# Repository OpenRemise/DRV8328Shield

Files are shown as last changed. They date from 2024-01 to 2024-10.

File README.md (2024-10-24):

# DRV8328Shield

RevA errors:
- PVDD should be tied to VIN instead of 5V  
  5V is simply too low to keep the high side switched on continuously

- TPS27S100B doesn't turn off if two consecutive shorts are too close together  
  This is also an issue for the ACK detection. The second ACK would simply get lost in this case:  
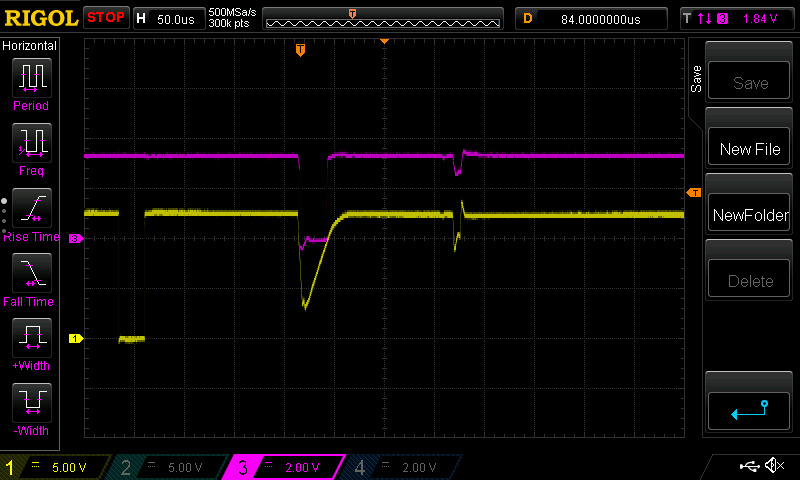
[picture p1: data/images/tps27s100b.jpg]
tps27s100b
    

  The only reliable fix for this might be to monitor IMON as well. Here is a capture of the second ACK pulse of an MX645 during a DECUP update. IMON is above 500mV for about 8µs.
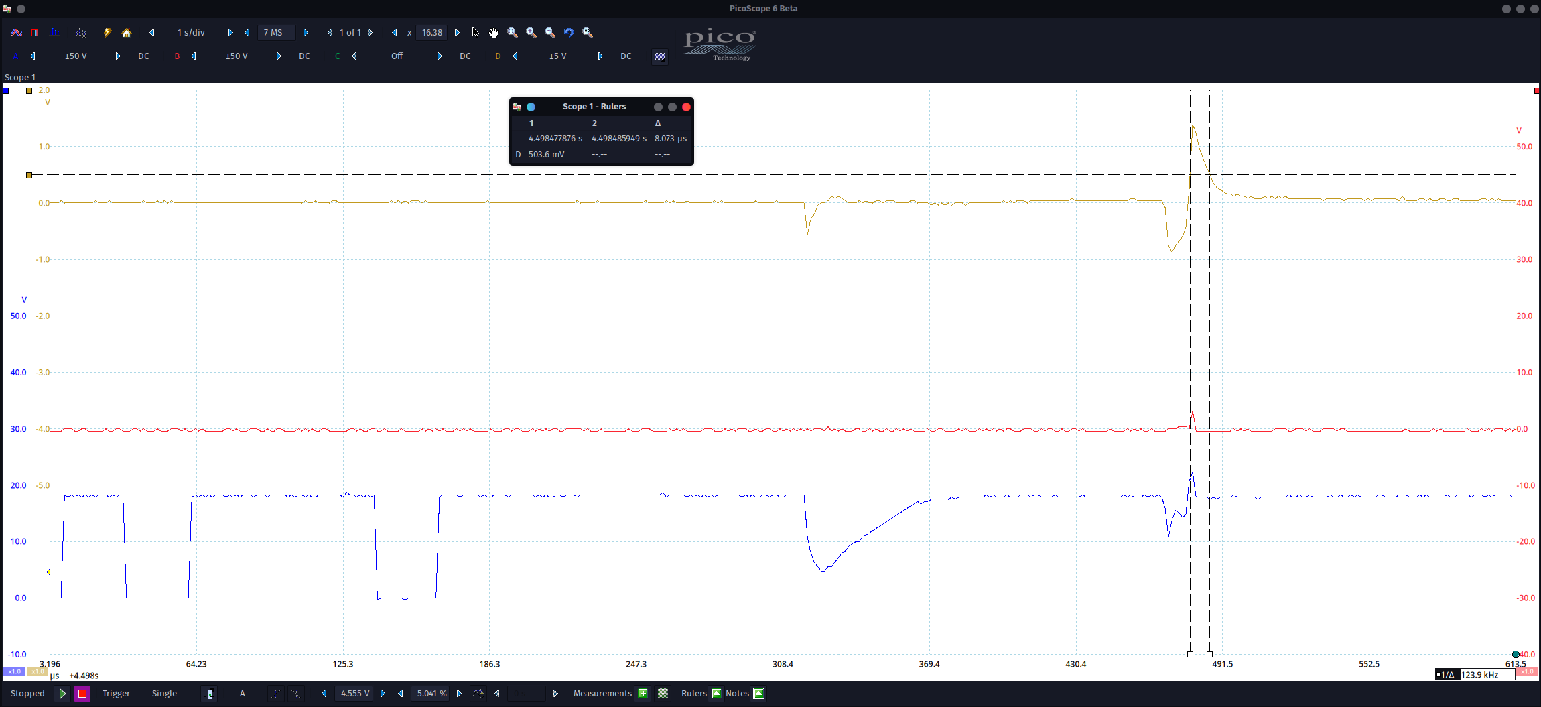
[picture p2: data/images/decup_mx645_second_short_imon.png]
decup_mx645_second_short_imon
    

  As it turns it this isn't a workaround either. While some shorts look like this  
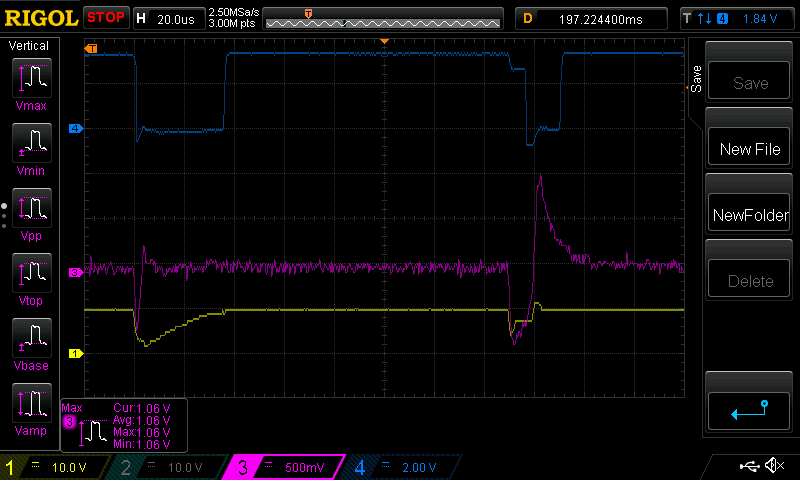
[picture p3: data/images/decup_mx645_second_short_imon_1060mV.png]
decup_mx645_second_short_imon_1060mV
    

  Others look like this  
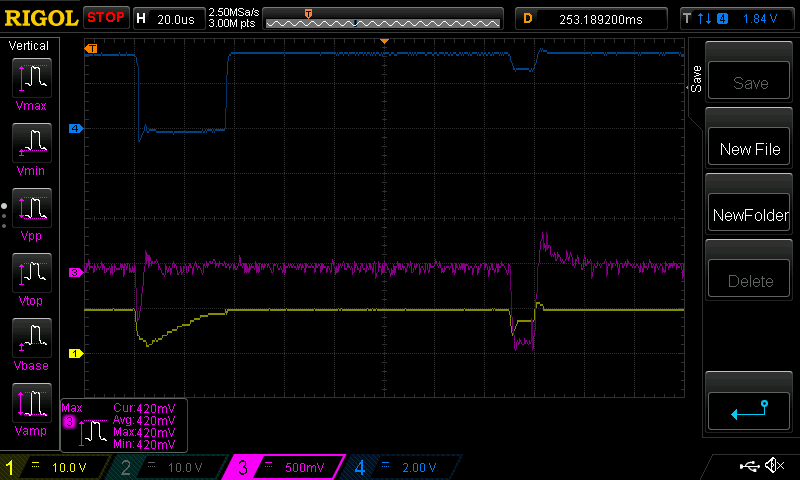
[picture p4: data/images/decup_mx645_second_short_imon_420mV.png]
decup_mx645_second_short_imon_420mV
    
  And that 420mV pulse is too short for a common LM339... now what?

- TPS27S100B could use another 1µF ceramic capacitor at IN (e.g. same as at OUT)

- N and P tracks are reversed  
  We currently generate the signal for INHA (output SHA) with the first half-bit 1 and the second half-bit 0. It must stay that way because we want the RMT end-of-transmission level to be 0. The problem is that a signal with the first half-bit 1 would mark the P and not the N track. Currently we feed SHA into the N pin though.  
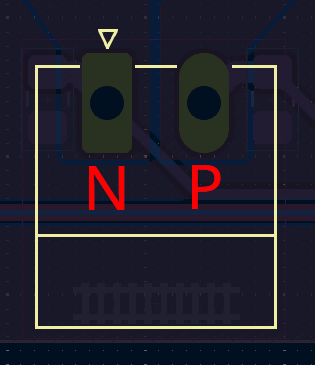
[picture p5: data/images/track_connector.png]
track


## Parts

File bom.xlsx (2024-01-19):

 |  |  | DRV8328Shield PCS BOM
Item # | *Designator | *Qty | Manufacturer | *Mfg Part # | Description / Value | *Package/Footprint | Type | Your Instructions / Notes
1 | C1, C5, C6, C14, C22 | 5 | Samsung Electro-Mechanics | CL05B104KB54PNC | CAP CER 0.1UF 50V X7R 0402 | 0402 | SMD
2 | C2, C4, C9, C10, C13, C18, C19, C21 | 8 | Murata Electronics | GRM1555C2A102JE01D | CAP CER 1000PF 100V C0G/NP0 0402 | 0402 | SMD
3 | C3 | 1 | Murata Electronics | GCM1555C1H221JA16D | CAP CER 220PF 50V C0G/NP0 0402 | 0402 | SMD
4 | C7, C8 | 2 | Murata Electronics | GCM1555C1H101JA16D | CAP CER 100PF 50V C0G/NP0 0402 | 0402 | SMD
5 | C11 | 1 | Murata Electronics | GRM31MR72A474KA35L | CAP CER 0.47UF 100V X7R 1206 | 1206 | SMD
6 | C12 | 1 | Samsung Electro-Mechanics | CL31B106KBHNNNE | CAP CER 10UF 50V X7R 1206 | 1206 | SMD
7 | C15, C23 | 2 | Nichicon | UCL1V101MCL6GS | CAP ALUM 100UF 20% 35V SMD | 6.60x6.60mm | SMD
8 | C16, C17, C20, C24 | 4 | Samsung Electro-Mechanics | CL31B105KCHVPJE | CAP CER 1UF 100V X7R 1206 | 1206 | SMD
9 | D1, D2, D4, D6, D7, D8, D9, D10, D11, D12 | 10 | onsemi | 1N4148WT | SMALL SIGNAL DIODE SOD523 100V | SOD-523 | SMD
10 | D3 | 1 | Diotec Semiconductor | BZX84C15 | DIODE ZENER 15V 300W SOT23-3 | SOT-23-3 | SMD
11 | D5 | 1 | Toshiba Semiconductor and Storage | CEZ30V,L3F | TVS DIODE 30VWM 47.5VC ESC | SOD-523
12 | J1 | 1 | Phoenix Contact | 1836189 | TERM BLOCK HDR 2POS 90DEG 5.08MM | not fitted | not fitted
13 | J2 | 1 | Phoenix Contact | 1844210 | TERM BLOCK HDR 2POS 90DEG 3.5MM | not fitted | not fitted
14 | J3 | 1 |  |  |  | not fitted | not fitted
15 | JP1 | 1 |  |  |  | not fitted | not fitted
16 | JP2 | 1 |  |  |  | not fitted | not fitted
17 | Q1, Q3, Q4, Q6, Q7 | 5 | Vishay Siliconix | SIS4634LDN-T1-GE3 | N-CHANNEL 60 V (D-S) MOSFET POWE | PowerPAK® 1212-8 | SMD
18 | Q2, Q8 | 2 | Rohm Semiconductor | QS6K21TR | MOSFET 2N-CH 45V 1A TSMT6 | TSOT-23-6 | SMD
19 | Q5, Q10 | 2 | ANBON SEMICONDUCTOR (INT'L) LIMITED | BC847B | PLASTIC ENCAPSULATE TRANSISTORS | SOT-23-3 | SMD
20 | Q9 | 1 | Diotec Semiconductor | BC857B | BJT SOT-23 45V 100MA | SOT-23-3 | SMD
21 | R1, R2, R3, R4, R43 | 5 | YAGEO | RC0402FR-0722KL | RES 22K OHM 1% 1/16W 0402 | 0402 | SMD
22 | R5, R11, R24, R26, R28, R34, R35, R45 | 8 | YAGEO | RC0402FR-0710KL | RES 10K OHM 1% 1/16W 0402 | 0402 | SMD
23 | R6, R7, R8 | 3 | YAGEO | RC0402FR-07100RL | RES 100 OHM 1% 1/16W 0402 | 0402 | SMD
24 | R9, R10, R36, R42, R44 | 5 | YAGEO | RC0402FR-074K7L | RES 4.7K OHM 1% 1/16W 0402 | 0402 | SMD
25 | R12 | 1 | Vishay Dale | RCS08052R20FKEA | RES SMD 2.2 OHM 1% 1/2W 0805 | 0805 | SMD
26 | R13, R14, R19, R27, R31, R37, R41 | 7 | YAGEO | RC0402FR-071KL | RES 1K OHM 1% 1/16W 0402 | 0402 | SMD
27 | R15, R18 | 2 | Stackpole Electronics Inc | RMCF0805FT4K70 | RES 4.7K OHM 1% 1/8W 0805 | not fitted | not fitted
28 | R16, R17 | 2 | YAGEO | RC0402FR-073K3L | RES 3.3K OHM 1% 1/16W 0402 | 0402 | SMD
29 | R20, R21 | 2 | YAGEO | RC0402FR-0733RL | RES 33 OHM 1% 1/16W 0402 | 0402 | SMD
30 | R22 | 1 | YAGEO | RC0402FR-13220RL | RES 220 OHM 1% 1/16W 0402 | 0402 | SMD
31 | R23, R25, R32, R33 | 4 | YAGEO | RC0402FR-0747RL | RES 47 OHM 1% 1/16W 0402 | 0402 | SMD
32 | R29 | 1 | YAGEO | RC0402FR-07100KL | RES 100K OHM 1% 1/16W 0402 | 0402 | SMD
33 | R30 | 1 | Stackpole Electronics Inc | RMCF0805FT220R | RES 220 OHM 1% 1/8W 0805 | 0805 | SMD
34 | R38 | 1 | YAGEO | RC0402FR-07120RL | RES 120 OHM 1% 1/16W 0402 | 0402 | SMD
35 | R39 | 1 | YAGEO | RC0402FR-072K2L | RES 2.2K OHM 1% 1/16W 0402 | 0402 | SMD
36 | R40 | 1 | YAGEO | RC0402FR-075K1L | RES 5.1K OHM 1% 1/16W 0402 | 0402 | SMD
37 | TP1, TP2, TP3, TP4, TP5, TP6, TP7, TP8, TP9, TP10, TP11, TP12 |  |  |  |  | not fitted | not fitted
38 | U1 | 1 | onsemi | LM393EDR2G | IC COMPARATOR 2 GEN PUR 8SOIC | 8-SOIC | SMD
39 | U2 | 1 | Nexperia USA Inc. | 74LVC02APW,118 | IC GATE NOR 4CH 2-INP 14TSSOP | 14-TSSOP | SMD
40 | U3 | 1 | Texas Instruments | TLV9051IDBVR | IC OPAMP GP 1 CIRCUIT SOT23-5 | SOT23-5 | SMD
41 | U4 | 1 | Texas Instruments | DRV8328BRUYR | 60 V 1000/2000 MA 3-PHASE GATE D | 28-WQFN | SMD
42 | U5 | 1 | Texas Instruments | TPS27S100BPWPR | IC PWR DRVR N-CHAN 1:1 14HTSSOP | 14-HTSSOP | SMD

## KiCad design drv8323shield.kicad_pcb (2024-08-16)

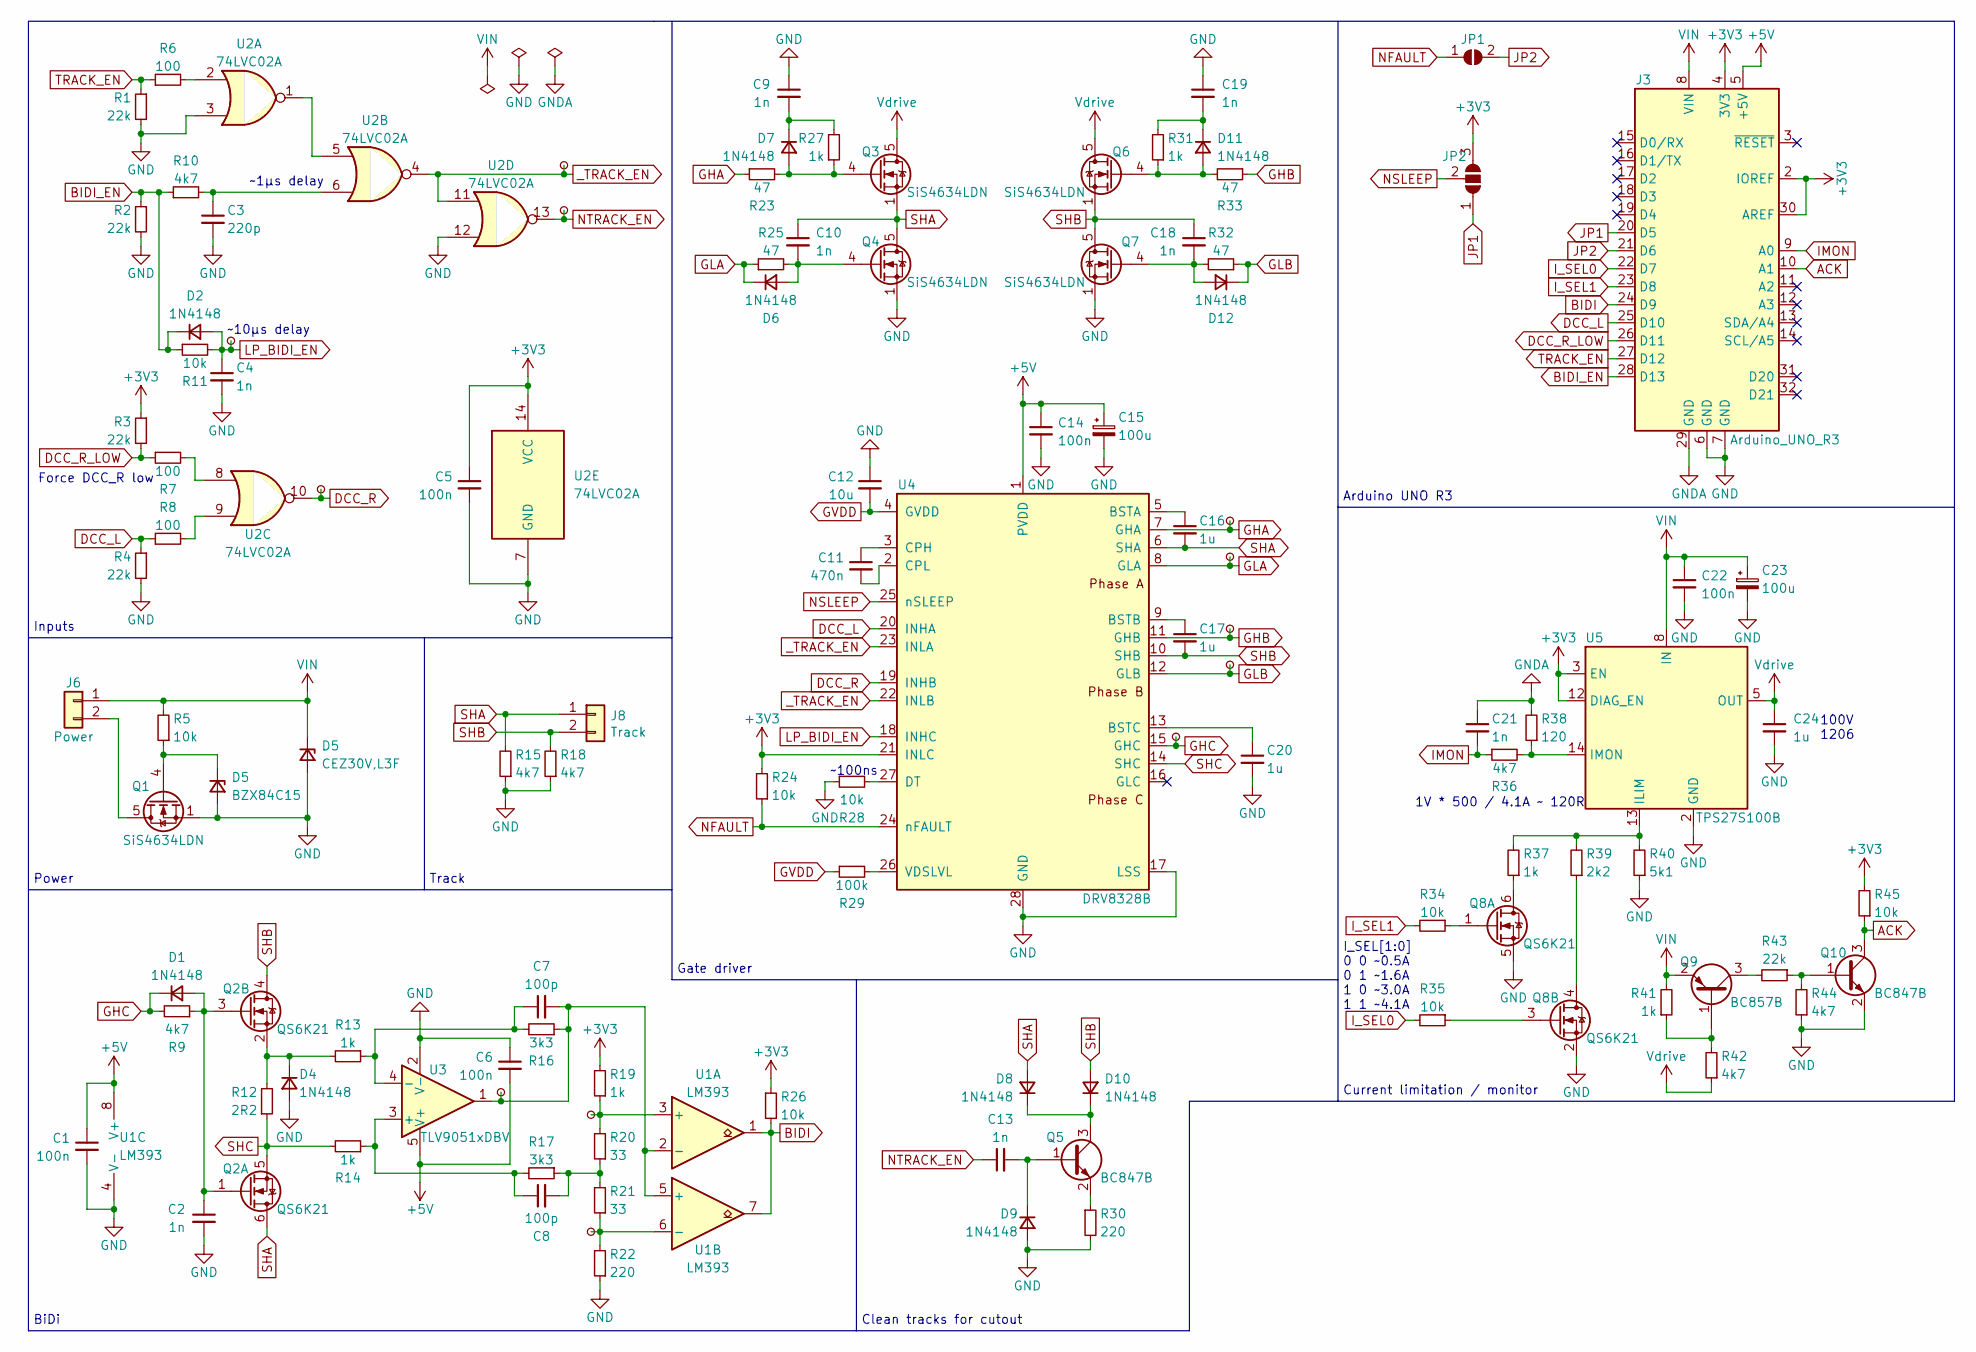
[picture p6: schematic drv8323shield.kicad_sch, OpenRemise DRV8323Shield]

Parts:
C1, C5, C6, C14, C22: 100n; C_0402_1005Metric
C2, C4, C9, C10, C13, C18, C19, C21: 1n; C_0402_1005Metric
C3: 220p; C_0402_1005Metric
C7, C8: 100p; C_0402_1005Metric
C11: 470n; C_1206_3216Metric
C12: 10u; C_1206_3216Metric
C15, C23: 100u; CP_Elec_6.3x7.7
C16, C17, C20, C24: 1u; C_1206_3216Metric
D1, D2, D4, D6, D7, D8, D9, D10, D11, D12: 1N4148; D_SOD-523
D5: CEZ30V,L3F; D_SOD-523
J3: Arduino_UNO_R3; Arduino_UNO_R3_WithMountingHoles
J6: Power; PhoenixContact_MC_1,5_2-G-5.08_1x02_P5.08mm_Horizontal
J8: Track; PhoenixContact_MC_1,5_2-G-3.5_1x02_P3.50mm_Horizontal
JP1: SolderJumper_2_Open; SolderJumper-2_P1.3mm_Open_Pad1.0x1.5mm
JP2: SolderJumper_3_Open; SolderJumper-3_P1.3mm_Open_Pad1.0x1.5mm
Q1, Q3, Q4, Q6, Q7: SiS4634LDN; Vishay_PowerPAK_1212-8_Single
Q2, Q8: QS6K21; TSOT-23-6
Q5, Q10: BC847B; SOT-23
Q9: BC857B; SOT-23-3
R1, R2, R3, R4, R43: 22k; R_0402_1005Metric
R5, R11, R24, R26, R28, R34, R35, R45: 10k; R_0402_1005Metric
R6, R7, R8: 100; R_0402_1005Metric
R9, R10, R36, R42, R44: 4k7; R_0402_1005Metric
R12: 2R2; R_0805_2012Metric_Pad1.20x1.40mm_HandSolder
R13, R14, R19, R27, R31, R37, R41: 1k; R_0402_1005Metric
R15, R18: 4k7; R_0805_2012Metric_Pad1.20x1.40mm_HandSolder
R16, R17: 3k3; R_0402_1005Metric
R20, R21: 33; R_0402_1005Metric
R22: 220; R_0402_1005Metric
R23, R25, R32, R33: 47; R_0402_1005Metric
R29: 100k; R_0402_1005Metric
R30: 220; R_0805_2012Metric_Pad1.20x1.40mm_HandSolder
R38: 120; R_0402_1005Metric
R39: 2k2; R_0402_1005Metric
R40: 5k1; R_0402_1005Metric
TP1, TP2, TP3, TP4, TP5, TP6, TP7, TP8, TP9, TP10, TP11, TP12: TestPoint_Small; TestPoint_Pad_1.0x1.0mm
U1: LM393; SOIC-8_3.9x4.9mm_P1.27mm
U2: 74LVC02A; TSSOP-14_4.4x5mm_P0.65mm
U3: TLV9051xDBV; SOT-23-5
U4: DRV8328B; QFN-28-1EP_4x4mm_P0.4mm_EP2.6x2.6mm_ThermalVias
U5: TPS27S100B; HTSSOP-14-1EP_4.4x5mm_P0.65mm_EP3.4x5mm_Mask3x3.1mm_Thermal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

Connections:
+3V3: C5.1, J3.2 (IOREF), J3.4 (3V3), J3.30 (AREF), JP2.3 (B), R3.1, R19.2, R24.2, R26.1, R45.2, U2.14 (VCC), U4.21 (INLC), U5.3 (EN), U5.12 (DIAG_EN)
+5V: C1.1, C6.2, C14.1, C15.1, J3.5 (+5V), U1.8 (V+), U3.5 (V+), U4.1 (PVDD)
ACK: J3.10 (A1), Q10.3 (C), R45.1
BIDI: J3.24 (D9), R26.2, U1.1, U1.7
BIDI_EN: D2.1 (K), J3.28 (D13), R2.1, R10.1, R11.1
DCC_L: J3.25 (D10), R4.1, R8.1, U4.20 (INHA)
DCC_R: TP2.1, U2.10, U4.19 (INHB)
DCC_R_LOW: J3.26 (D11), R3.2, R7.1
GHA: R23.1, TP9.1, U4.7 (GHA)
GHB: R33.1, TP11.1, U4.11 (GHB)
GHC: D1.1 (K), R9.2, TP8.1, U4.15 (GHC)
GLA: D6.1 (K), R25.1, TP10.1, U4.8 (GLA)
GLB: D12.1 (K), R32.1, TP12.1, U4.12 (GLB)
GND: C1.2, C2.2, C3.2, C4.2, C5.2, C6.1, C9.1, C12.1, C14.2, C15.2, C19.1, C20.2, C22.2, C23.2, C24.2, D4.2 (A), D5.2 (A), D9.2 (A), J3.6 (GND), J3.7 (GND), Q1.1 (S), Q1.2 (S), Q1.3 (S), Q4.1 (S), Q4.2 (S), Q4.3 (S), Q7.1 (S), Q7.2 (S), Q7.3 (S), Q8.2 (S), Q8.5 (S), Q10.2 (E), R1.2, R2.2, R4.2, R15.1, R18.1, R22.1, R28.1, R30.2, R40.1, R44.1, U1.4 (V-), U2.3, U2.7 (GND), U2.12, U3.2 (V-), U4.17 (LSS), U4.28 (GND), U4.29 (GND), U5.2 (GND), U5.15 (GND); also elsewhere on the board
GNDA: C21.1, J3.29 (GND), R38.2
GVDD: C12.2, R29.1, U4.4 (GVDD)
IMON: C21.2, J3.9 (A0), R36.1
I_SEL0: J3.22 (D7), R35.2
I_SEL1: J3.23 (D8), R34.2
JP1: J3.20 (D5), JP2.1 (A)
JP2: J3.21 (D6), JP1.2 (B)
LP_BIDI_EN: C4.1, D2.2 (A), R11.2, TP1.1, U4.18 (INHC)
NFAULT: JP1.1 (A), R24.1, U4.24 (nFAULT)
NSLEEP: JP2.2 (C), U4.25 (nSLEEP)
NTRACK_EN: C13.1, TP5.1, U2.13
unnamed: C3.1, R10.2, U2.6
unnamed: C8.2, R17.1, R20.1, R21.2
unnamed: C2.1, D1.2 (A), Q2.1 (G), Q2.3 (G), R9.1
unnamed: D4.1 (K), Q2.2 (S), R12.2, R13.2
unnamed: C10.2, D6.2 (A), Q4.4 (G), R25.2
unnamed: D7.2 (A), Q3.4 (G), R23.2, R27.1
unnamed: C9.2, D7.1 (K), R27.2
unnamed: C13.2, D9.1 (K), Q5.1 (B)
unnamed: D8.1 (K), D10.1 (K), Q5.3 (C)
unnamed: D11.2 (A), Q6.4 (G), R31.1, R33.2
unnamed: C19.2, D11.1 (K), R31.2
unnamed: C18.2, D12.2 (A), Q7.4 (G), R32.2
unnamed 37: Q1.5 (D); also elsewhere on the board
unnamed: Q5.2 (E), R30.1
unnamed: Q8.6 (D), R37.1
unnamed: Q8.1 (G), R34.1
unnamed: Q8.4 (D), R39.1
unnamed: Q8.3 (G), R35.1
unnamed: Q9.1 (B), R41.1, R42.2
unnamed: Q9.3 (C), R43.2
unnamed: Q10.1 (B), R43.1, R44.2
unnamed: R6.2, U2.2
unnamed: R7.2, U2.8
unnamed: R8.2, U2.9
unnamed: R19.1, R20.2, TP6.1, U1.3 (+)
unnamed: C7.2, R16.1, TP3.1, U1.2 (-), U1.5 (+), U3.1
unnamed: R21.1, R22.2, TP7.1, U1.6 (-)
unnamed: U2.1, U2.5
unnamed: C8.1, R14.1, R17.2, U3.3 (+)
unnamed: C7.1, R13.1, R16.2, U3.4 (-)
unnamed: C16.1, U4.5 (BSTA)
unnamed: C17.1, U4.9 (BSTB)
unnamed: C20.1, U4.13 (BSTC)
unnamed: C11.1, U4.3 (CPH)
unnamed: C11.2, U4.2 (CPL)
unnamed: R28.2, U4.27 (DT)
unnamed: R29.2, U4.26 (VDSLVL)
unnamed: R37.2, R39.2, R40.2, U5.13 (ILIM)
unnamed: R36.2, R38.1, U5.14 (IMON)
SHA: C10.1, C16.2, D8.2 (A), Q2.6 (D), Q3.1 (S), Q3.2 (S), Q3.3 (S), Q4.5 (D), R15.2, U4.6 (SHA); also elsewhere on the board
SHB: C17.2, C18.1, D10.2 (A), Q2.4 (D), Q6.1 (S), Q6.2 (S), Q6.3 (S), Q7.5 (D), R18.2, U4.10 (SHB); also elsewhere on the board
SHC: Q2.5 (S), R12.1, R14.2, U4.14 (SHC)
TRACK_EN: J3.27 (D12), R1.1, R6.1
Vdrive: C24.1, Q3.5 (D), Q6.5 (D), R42.1, U5.5 (OUT), U5.6 (OUT), U5.7 (OUT)
_TRACK_EN: TP4.1, U2.4, U2.11, U4.22 (INLB), U4.23 (INLA)

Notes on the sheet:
Track
Inputs
Clean tracks for cutout
~10µs delay
BiDi
1V * 500 / 4.1A ~ 120R
Gate driver
Current limitation / monitor
100V 1206
Power
Force DCC_R low
~100ns
I_SEL[1:0] 0 0 ~0.5A 0 1 ~1.6A 1 0 ~3.0A 1 1 ~4.1A
Arduino UNO R3
~1µs delay

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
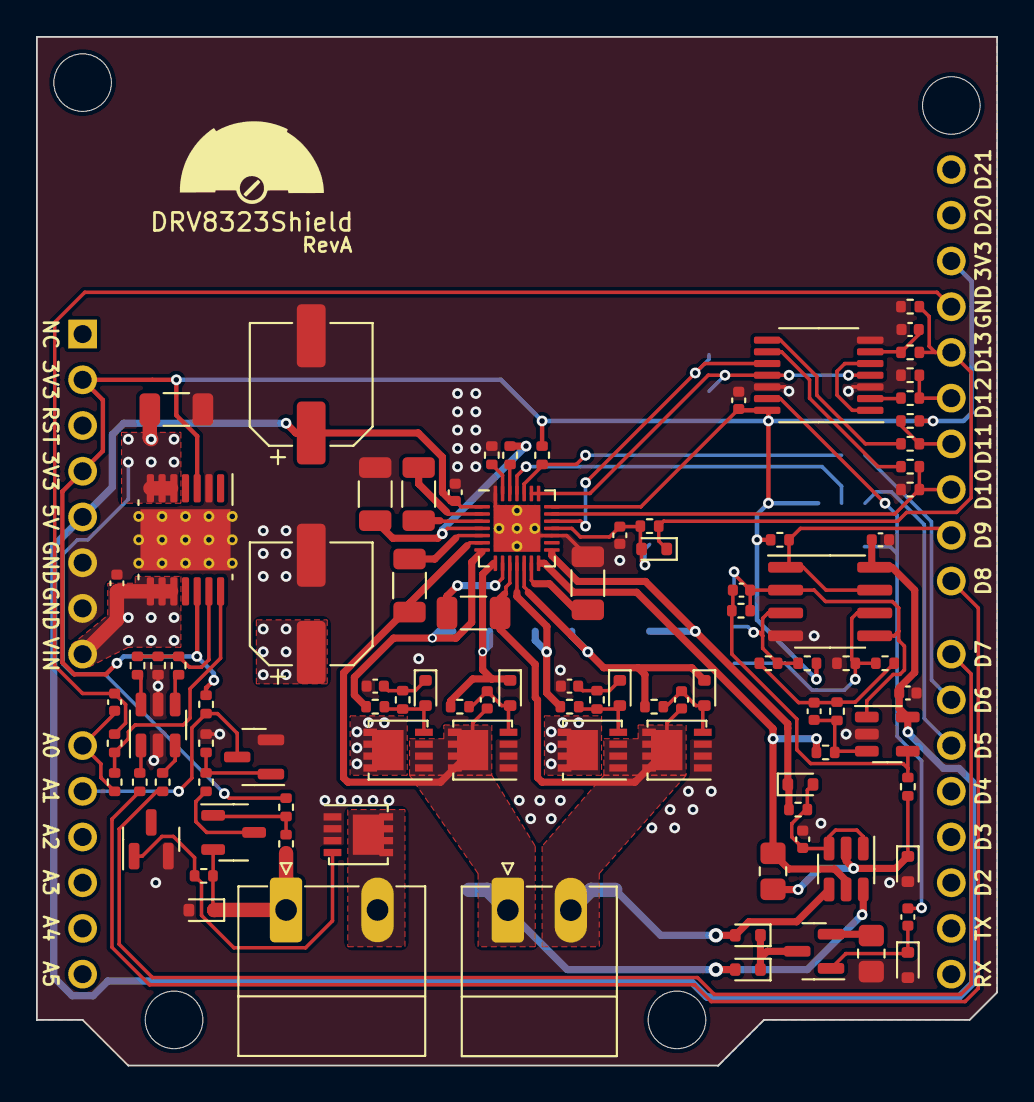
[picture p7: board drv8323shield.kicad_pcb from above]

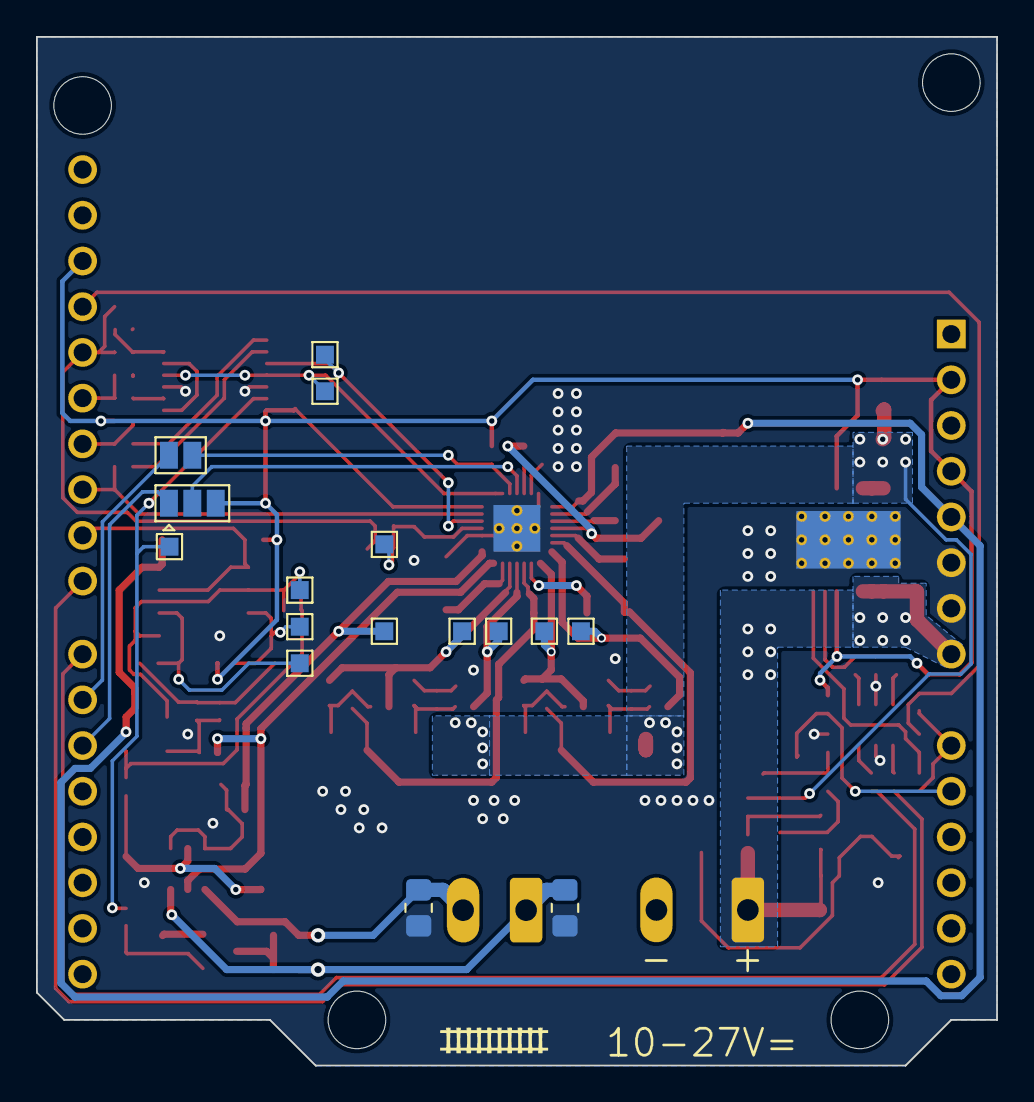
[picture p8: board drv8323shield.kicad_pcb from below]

Board: 2 copper layers, 53.3 x 57.2 mm, 113 parts (17 on the bottom side), 72 nets.

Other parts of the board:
D3: BZX84C15; SOT-23
J1: Power; PhoenixContact_MC_1,5_2-G-5.08_1x02_P5.08mm_Horizontal
J2: Track; PhoenixContact_MC_1,5_2-G-3.5_1x02_P3.50mm_Horizontal

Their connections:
GND: D3.2 (A); also elsewhere on the board
unnamed 37: J1.2; also elsewhere on the board
SHA: J2.1; also elsewhere on the board
SHB: J2.2; also elsewhere on the board

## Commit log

2024-01-19 Order RevA
    [bom.xlsx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]
2024-08-16 chore: migrate to KiCad 8.0
    [drv8323shield.kicad_pcb, drv8323shield.kicad_sch]
